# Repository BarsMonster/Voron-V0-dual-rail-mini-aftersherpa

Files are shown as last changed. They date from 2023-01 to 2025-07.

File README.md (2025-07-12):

# Voron V0 - dual rail mod for Mini-AfterSherpa
One of the limitations on the path to better print quality, higher accelerations, less ringing is rigidity of the printer. Weakest point in Voron V0 is arguably X-rail carriage. I believe that dual MGN7 offers more rigidity / less play than even single MGN9 rail due to less "amplification of backlash". In my view the only competing single-rail approach offering similar rigidity is Pandora-style rail mount on the front (https://github.com/MasturMynd/Pandora), preferably with wide rail (MGW7 / MGW9) - but it requires significantly more changes to the printer. 

I've tried 3 different single MGN7 rails with medium preload from different suppliers and was never satisfied with hotend wiggle. This mod dramatically increases rigidity, so that on resonance tower I no longer see much  ringing even without input shaping (=sharper, faster, higher quality prints). 

Original dual rail mod by [@camerony](https://github.com/camerony) (https://github.com/camerony/VoronCustom/tree/main/V0.1_Dual_X_Rail_Carriage) is not compatible with Mini-AfterSherpa (https://github.com/PrintersForAnts/Mini-AfterSherpa) - as it lowers mount point too much, so extruder would collide with the X bracket (unless you install extruder backwards which will severely limit Y travel range). 

In this mod - bracket is redesigned, mount points are shifted up 2mm.
As rigidity of dual rail is much higher than needed - feel free to reduce infill to 25% and perimeters to 3 in the bracket if you want to save ~1g.

Thickness of bottom part of the bracket is reduced to 2mm to make it easier to clear extrusions of Z axis. 

# Travel range
* XY travel range is unaffected. 
* Z travel range is increased by 2mm. 
* Free space above carriage is reduced by 2mm, so you will benefit with any of tophat mods with more space. 

# Homing
It only supports sensorless homing on X axis. If we are saving weight - we must drop X endstop. 
As motors might slightly touch bottom carriage - homing procedure must be changed:

* Home Y axis first, then go to Y coordinate 60
* Home X axis, then go to X coordinate 60
* Do final Y axis homing

This will ensure reliable homing regardless on position where it was left before. Triple homing is slower, but you can do it while heating up. Alternatively, you can add ~1mm spacers to make sure Y axis stops slightly before carriage can touch motors. Example sensorless homing config macro is included. 

Alternatively, one can home to Y0 instead of Ymax. 

# Requires
* Second 150mm MGN7 rail with MGN7H carriage, medium preload. 
* 10xM2 nuts and 10x M2x6mm screws to mount secondary rail, print 1x standard nut carrier. 
* Mod to raise X rail by 4mm : https://github.com/camerony/VoronCustom/tree/main/V0.1_Raise_X_Axis_Extrusion_by_4mm
* 4x M2x5mm or M2x6mm screws to mount bottom rail. Recommended to get ultrathin ones, as it's quite tight on the bottom. If screws hit extrusions, and you only have regular hex screws - you can sand them down by ~0.5mm to make thinner head.
* 2x M3 heat inserts

# Resonance comparison
Note different amplitude scale. Recommended acceleration is 5x better. More prominent difference in on X, on Y everything is too wobly on single rail. It is possible that with higher-quality rails difference would be less dramatic : 

**Single rail:**

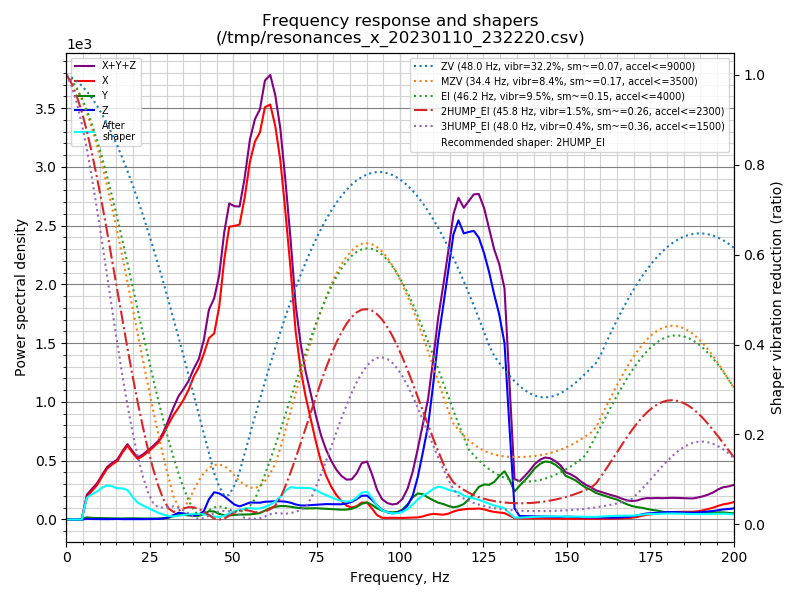
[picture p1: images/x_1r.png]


**Double rail:**

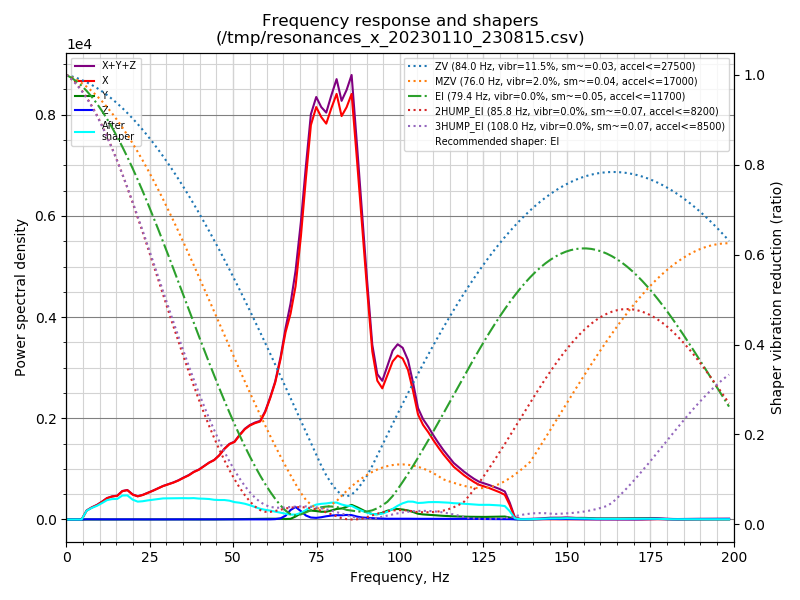
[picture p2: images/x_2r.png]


# Photos

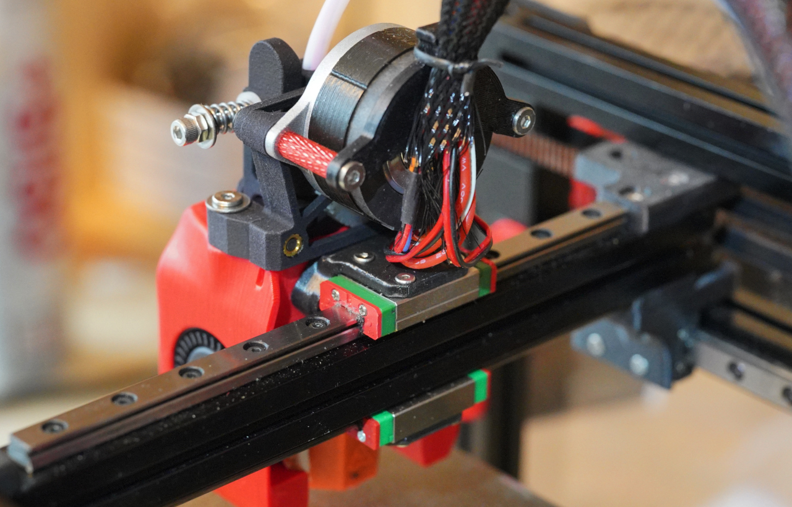
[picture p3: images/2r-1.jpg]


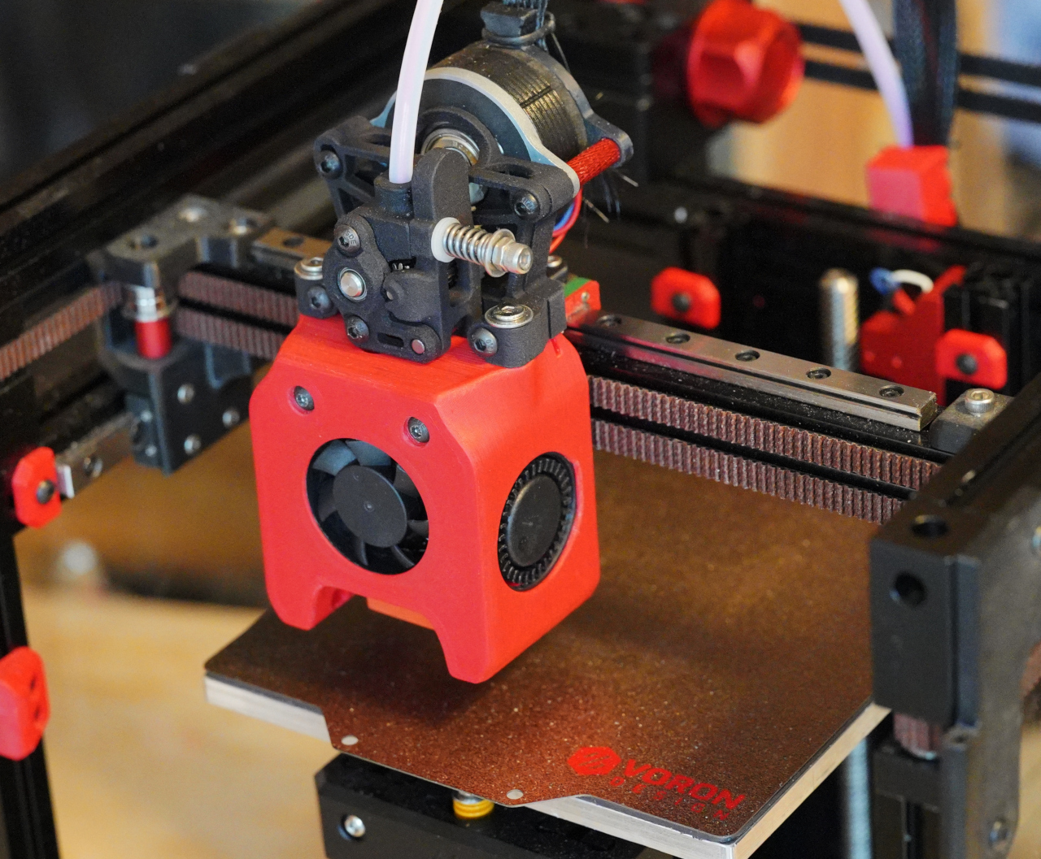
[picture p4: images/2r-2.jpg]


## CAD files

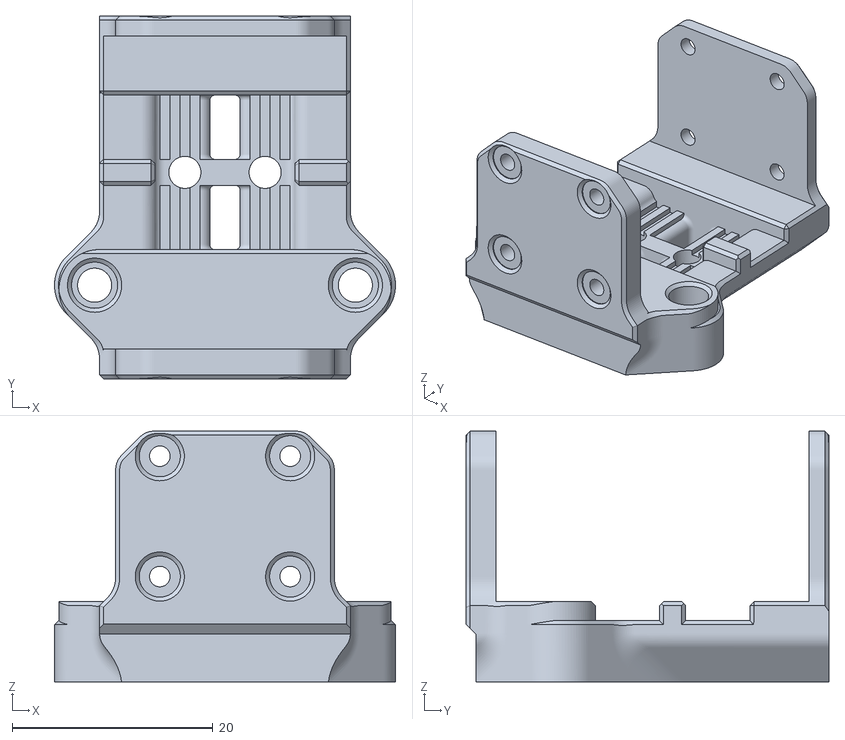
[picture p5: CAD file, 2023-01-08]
V0-dual-rail-bracket.stl
34.0 x 36.2 x 25.0

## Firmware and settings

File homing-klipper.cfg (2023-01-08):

[homing_override]
#set_position_z: 5
#gcode:
  #G90          # Absolute positioning
  #G1 Z5 F3000  # Move Z up
  #SENSORLESS_HOME_X
  #SENSORLESS_HOME_Y
  #G1 X0.8 Y0.8 F6000
  ##G1 X{ printer.toolhead.axis_maximum.x / 2 } Y{ printer.toolhead.axis_maximum.y / 2 } F{ printer.toolhead.max_velocity * 60 }
  #G28 Z F3000  # Home Z
  #G1 Z5 F6000  # Move Z up
axes: xyz
gcode:
  {% set home_all = 'X' not in params and 'Y' not in params and 'Z' not in params %}
  force_move stepper=stepper_z distance=5 velocity=10 accel=300
  {% if home_all or 'Y' in params %}
    SENSORLESS_HOME_Y
  {% endif %}

  {% if home_all or 'X' in params %}
    SENSORLESS_HOME_X
  {% endif %}
  
  #homing second time to ensure we are perfectly homed on Y
  {% if home_all or 'Y' in params %}
    G1 X60 Y110 F12000
    SENSORLESS_HOME_Y
  {% endif %}
  
  {% if home_all or 'Z' in params %}
#    G28 Z
#    G1 Z10
  G90 #absolute
  G1 X0.8 Y0.8 F12000
  #G1 X{ printer.toolhead.axis_maximum.x / 2 } Y{ printer.toolhead.axis_maximum.y / 2 } F{ printer.toolhead.max_velocity * 60 }
  G28 Z F3000  # Home Z
  G1 Z5 F6000  # Move Z up
  {% endif %}

[gcode_macro SENSORLESS_HOME_X]
gcode:
    {% set driver_config = printer.configfile.settings['tmc2209 stepper_x'] %}
    {% set RUN_CUR = driver_config.run_current %}
    #{% set HOME_CUR = RUN_CUR * 0.700 %}
    {% set HOME_CUR = 0.34 %}
    # Set current for sensorless homing
    SET_TMC_CURRENT STEPPER=stepper_x CURRENT={HOME_CUR}
    SET_TMC_CURRENT STEPPER=stepper_y CURRENT={HOME_CUR}
    M204 P1000 T500
    # Pause to ensure driver stall flag is clear
    G4 P500
    # Home
    G91
    G28 X
    # Move away
    G90 # Absolute positioning
    G1 X60 F12000
    # Set current during print
    SET_TMC_CURRENT STEPPER=stepper_x CURRENT={RUN_CUR}
    SET_TMC_CURRENT STEPPER=stepper_y CURRENT={RUN_CUR}

[gcode_macro SENSORLESS_HOME_Y]
gcode:
    {% set driver_config = printer.configfile.settings['tmc2209 stepper_x'] %}
    {% set RUN_CUR = driver_config.run_current %}
    #{% set HOME_CUR = RUN_CUR * 0.700 %}
    {% set HOME_CUR = 0.34 %}
    # Set current for sensorless homing
    SET_TMC_CURRENT STEPPER=stepper_x CURRENT={HOME_CUR}
    SET_TMC_CURRENT STEPPER=stepper_y CURRENT={HOME_CUR}
    M204 P1000 T500
    # Pause to ensure driver stall flag is clear
    G4 P500
    # Home
    G91
    G28 Y
    # Move away
    G90
    G1 Y60 F12000
    # Set current during print
    SET_TMC_CURRENT STEPPER=stepper_x CURRENT={RUN_CUR}
    SET_TMC_CURRENT STEPPER=stepper_y CURRENT={RUN_CUR}

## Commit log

2023-01-08 Final version of stl
    [V0-dual-rail-bracket.stl]
2023-01-08 Fix stl - apparently broken normals from Cura
    [V0-dual-rail-bracket.stl]
